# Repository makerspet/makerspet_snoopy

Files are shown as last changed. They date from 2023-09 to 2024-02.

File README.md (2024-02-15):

# Snoopy pet robot



An open-source 300mm DIY 3D-printable pet robot compatible with [Kaia.ai](https://kaia.ai) software [platform](https://github.com/kaiaai/).

Snoopy was designed in Fusion 360 in 05/2023 and printed using a Voron 2.4r2 350mm.

3D print, build, run and mod your own home pet robot! Please learn more at [Maker's Pet](https://makerspet.com).

## Features
- room mapping using a 360-degree laser distance sensor (ROS2-based).
- fully autonomous navigation (ROS2-based).
- code your character, skills (work in progress)
- 3D-printable, 300mm round base
- A smartphone or a 7" tablet acts as a color camera, head display.
- Arduino ESP32 micro-controller.
- optional: 2 bumpers, 4 bumper sensors, 5 cliff sensors.

## Assembly instructions video (Loki, Fido models)
<a href="http://www.youtube.com/watch?feature=player_embedded&v=WPB2B1DPf_s" target="_blank">
 Watch the assembly instructions video
</a>

## PC, firmware setup instructions video
<a href="http://www.youtube.com/watch?feature=player_embedded&v=XOc5kCE3MC0" target="_blank">
 Watch the one-time PC setup, firmware upload instructions video
</a>

## Bring-up instructions video
<a href="http://www.youtube.com/watch?feature=player_embedded&v=L_XbkA4pwRc" target="_blank">
 Watch the bring-up instructions video
</a>

## 3D printing instructions
<a href="http://www.youtube.com/watch?feature=player_embedded&v=4k6W1QyJMMw" target="_blank">
 Watch the bring-up instructions video
</a>

## Arduino ESP32 breakout board setup instructions
<a href="http://www.youtube.com/watch?feature=player_embedded&v=zizGI8MjANU" target="_blank">
 Watch the Arduino ESP32 breakout board setup instructions video
</a>



PXL_20230609_174802983-scaled

PXL_20230530_031143988-scaled

PXL_20230530_021024946-scaled

## Instructions and files
- 3D printing [STL](https://github.com/makerspet/3d_models/tree/main/snoopy_300mm/stl), [3MF](https://github.com/makerspet/3d_models/tree/main/snoopy_300mm/3mf)
- Arduino ESP32 [firmware](https://github.com/kaiaai/firmware)
- PC end user and developer [setup](https://github.com/kaiaai/docker)
- KiCad [schematic, PCB](https://github.com/makerspet/pcb)
- Software setup, configuration [instructions](https://www.youtube.com/playlist?list=PLOSXKDW70aR8SA16wTB0ou9ClKhv7micy)
- Fusion 360 3D CAD [design files](https://github.com/makerspet/3d_models/tree/main/snoopy_300mm/fusion360)
- ROS2 software mod [instructions](https://github.com/makerspet/makerspet_loki/tree/main/urdf)

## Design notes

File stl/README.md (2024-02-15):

Please find 3D model files here https://github.com/makerspet/3d_models/tree/main/snoopy_300mm/stl/.

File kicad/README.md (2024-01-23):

Please find PCB files here https://github.com/makerspet/pcb/.

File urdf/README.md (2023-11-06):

# Maker's Pet Snoopy robot model and configurations

## Modding the robot
- Clone `makerspet_snoopy` robot into a new `jacks_droid` robot.
```
cp -r /ros_ws/src/makerspet_snoopy /ros_ws/src/jacks_droid
rm -rf /ros_ws/src/jacks_droid/.git
```
- Edit `jacks_droid/package.xml` to update the author, website, description, version, email
- Edit `jacks_droid/README.md` to update the description
- Edit `jacks_droid/sdf/jacks_droid/model.config` to update the author, description, version, email
- If needed, edit the robot config files in `jacks_robot/config/`
- If needed, edit the robot model in `jacks_droid/urdf/robot.urdf.xacro`
- Regenerate your simulation model and compile your `jacks_droid` description
```
ros2 run kaiaai_gazebo urdf2sdf.sh /ros_ws/src/jacks_droid
cd /ros_ws
colcon build --symlink-install --packages-select jacks_droid
```

## Command cheat sheet

Operate a modded pet robot residing in `jacks_droid` repo:

```
# Launch the physical robot
ros2 launch kaiaai_bringup physical.launch.py robot_model:=jacks_droid

# Monitor robot's sensors
ros2 launch kaiaai_bringup rviz2.launch.py robot_model:=jacks_droid

# Launch the robot in a simulation - drive manually or let it self-drive
ros2 launch kaiaai_gazebo world.launch.py robot_model:=jacks_droid
ros2 run kaiaai_teleop teleop_keyboard robot_model:=jacks_droid
ros2 launch kaiaai_gazebo self_drive_gazebo.launch.py robot_model:=jacks_droid
ros2 launch kaiaai_bringup rviz2.launch.py robot_model:=jacks_droid

# Launch the robot in a simulation - create, save a map
ros2 launch kaiaai_gazebo world.launch.py robot_model:=jacks_droid
ros2 launch kaiaai_bringup cartographer.launch.py use_sim_time:=true robot_model:=jacks_droid
ros2 launch kaiaai_gazebo self_drive_gazebo.launch.py robot_model:=jacks_droid
ros2 run nav2_map_server map_saver_cli -f $HOME/my_map

# Launch the robot in a simulation - let it navigate automatically using an existing map
ros2 launch kaiaai_gazebo world.launch.py robot_model:=jacks_droid
ros2 launch kaiaai_bringup navigation.launch.py use_sim_time:=true map:=$HOME/my_map.yaml robot_model:=jacks_droid

# Inspect or edit robot's URDF model - useful when modding a robot
ros2 launch kaiaai_bringup inspect_urdf.launch.py robot_model:=jacks_droid
ros2 launch kaiaai_bringup edit_urdf.launch.py robot_model:=jacks_droid

# Convert URDF robot model file into SDF Gazebo simulation model file
ros2 run kaiaai_gazebo urdf2sdf.sh /ros_ws/src/jacks_droid
cd /ros_ws && colcon build --symlink-install --packages-select jacks_droid
```

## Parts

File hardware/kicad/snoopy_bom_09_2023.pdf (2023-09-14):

Maker's Pet Snoopy | https://makerspet.com Electronics BOM, version 9/2023
# | ReferenceQty Value | Footprint DNP | URL

1 J1 | 1 JST PH 8-pin male
2 J2, J5 | 2 JST XH 5-pin male
3 J3 | 1 Deans T-Plug Male | https://www.aliexpress.us/item/2251832807355213.html
4 R1, R3 | 2 10k | 603
5 R5 | 1 200k | 603
6 R6 | 1 100k | 603
7 U1 | 1 ESP32 DEV KIT DOIT 30-pin
8 U2 | 1 MH-KC24 | USB step-down module 24V dual output | https://www.aliexpress.us/item/3256802247317350.html

EXTERNAL COMPONENTS
1 | 2 CHR-GM25-BLDC2418 | BLDC motors 2.5W 190RPM rated 0.35A stall https://www.aliexpress.us/item/2251832633601682.html
2 | 1 YDLIDAR X4 | Laser distance scanner | https://www.ydlidar.com/
3 1 24V battery, Deans T-Plug Female plug Alcaline non-reusable or lithium 6S >=5A load

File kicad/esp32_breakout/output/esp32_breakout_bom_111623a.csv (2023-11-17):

Source: | C:\Users\ilya\git\snoopy\kicad\esp32_breakout\esp32_breakout.kicad_sch
Date: | 11/16/2023 7:33:45 PM
Tool: | Eeschema 7.0.9
Generator: | C:\Program Files\KiCad\7.0\bin\scripting\plugins/bom_csv_grouped_by_value_with_fp.py
Component Count: | 30
Ref | Qnty | Value | Cmp name | Footprint | Description | Vendor | DNP
D1 | 1 | CGRA4004-G | D | Diode_SMD:D_SMA | Diode
H1, H2, H3, H4 | 4 | MountingHole | MountingHole | MountingHole:MountingHole_3.2mm_M3 | Mounting Hole without connection
J1, J2 | 2 | JST PH F | Conn_01x05 | Connector_JST:JST_PH_B5B-PH-K_1x05_P2.00mm_Vertical | Generic connector, single row, 01x05, script generated (kicad-library-utils/schlib/autogen/connector/)
J3 | 1 | JST PH F | Conn_01x07 | Connector_JST:JST_PH_B7B-PH-K_1x07_P2.00mm_Vertical | Generic connector, single row, 01x07, script generated (kicad-library-utils/schlib/autogen/connector/)
J4 | 1 | DC-005 5.5x2.1mm | Barrel_Jack_Switch | Connector_BarrelJack:BarrelJack_GCT_DCJ200-10-A_Horizontal | DC Barrel Jack with an internal switch
J5 | 1 | Deans T-Plug M | Deans T-Plug | Makerspet:DEANS-T-PLUG
J6 | 1 | Header F | Conn_02x04_Top_Bottom | Connector_PinHeader_2.54mm:PinHeader_2x04_P2.54mm_Vertical | Generic connector, double row, 02x04, top/bottom pin numbering scheme (row 1: 1...pins_per_row, row2: pins_per_row+1 ... num_pins), script generated (kicad-library-utils/schlib/autogen/connector/)
J7 | 1 | Header F | Conn_01x05 | Connector_PinHeader_2.54mm:PinHeader_1x05_P2.54mm_Vertical | Generic connector, single row, 01x05, script generated (kicad-library-utils/schlib/autogen/connector/)
J8 | 1 | Header F | Conn_01x03 | Connector_PinHeader_2.54mm:PinHeader_1x03_P2.54mm_Vertical | Generic connector, single row, 01x03, script generated (kicad-library-utils/schlib/autogen/connector/)
J9, J10, J11 | 3 | JST PH F | Conn_01x06 | Connector_JST:JST_PH_B6B-PH-K_1x06_P2.00mm_Vertical | Generic connector, single row, 01x06, script generated (kicad-library-utils/schlib/autogen/connector/)
Q1 | 1 | BSS123 | BSS123 | Package_TO_SOT_SMD:SOT-23 | 0.17A Id, 100V Vds, N-Channel MOSFET, SOT-23
R1, R2, R3, R4, R6, R7 | 6 | 10k | R_Small_US | Resistor_SMD:R_0603_1608Metric | Resistor, small US symbol
R5 | 1 | 1k | R_Small_US | Resistor_SMD:R_0603_1608Metric | Resistor, small US symbol
R8 | 1 | 200k | R_Small_US | Resistor_SMD:R_0603_1608Metric | Resistor, small US symbol
R9 | 1 | 100k | R_Small_US | Resistor_SMD:R_0603_1608Metric | Resistor, small US symbol
R10 | 1 | 4.7k | R_Small_US | Resistor_SMD:R_0603_1608Metric | Resistor, small US symbol
SW1 | 1 | SS12D10 | SW_SPDT | Makerspet:SWITCH | Switch, single pole double throw
U1 | 1 | ESP32 DEV KIT 30-pin | ESP32-DOIT-V1 | Makerspet:ESP-32
U2 | 1 | Mini560-Pro | DC-DC | Makerspet:Mini560-Pro

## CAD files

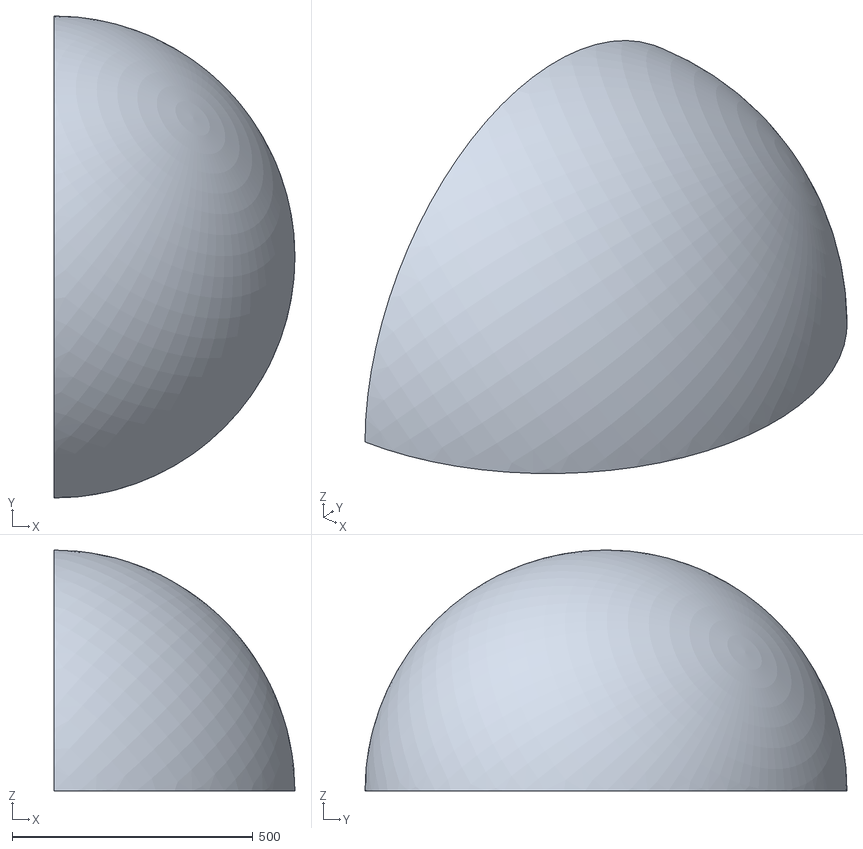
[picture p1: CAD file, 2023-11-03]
sdf/makerspet_snoopy/mesh/quarter_sphere.stl
500.0 x 1000.0 x 500.0

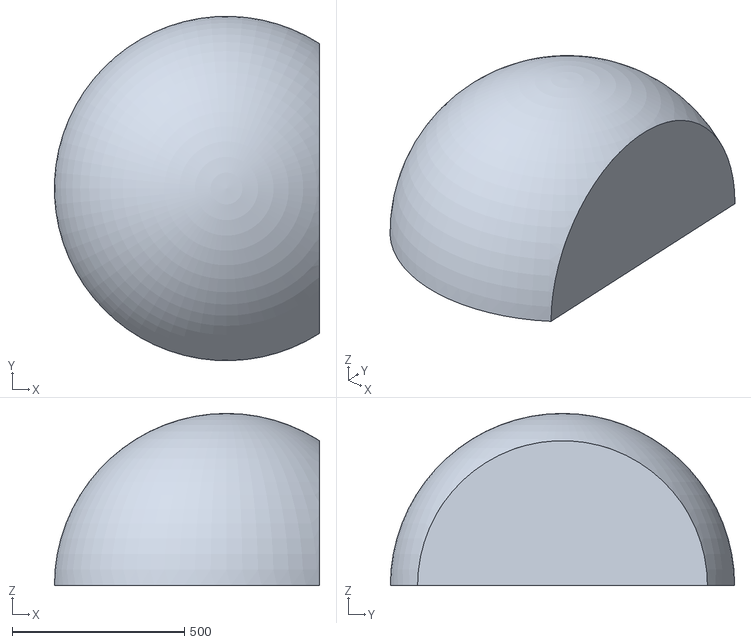
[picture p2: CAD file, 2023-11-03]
sdf/makerspet_snoopy/mesh/head.stl
769.5 x 999.7 x 500.0

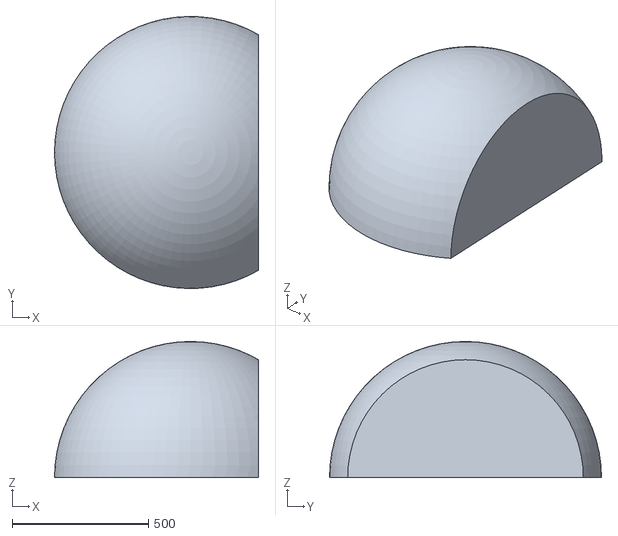
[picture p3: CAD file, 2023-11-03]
sdf/makerspet_snoopy/mesh/quarter_sphere_250mm.stl
750.0 x 999.7 x 500.0

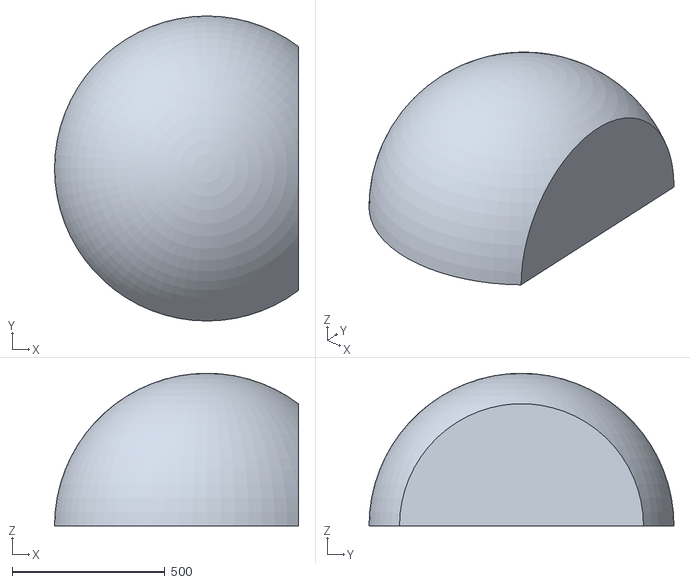
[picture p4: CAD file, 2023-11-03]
sdf/makerspet_snoopy/mesh/quarter_sphere_300mm.stl
800.0 x 1000.0 x 500.0

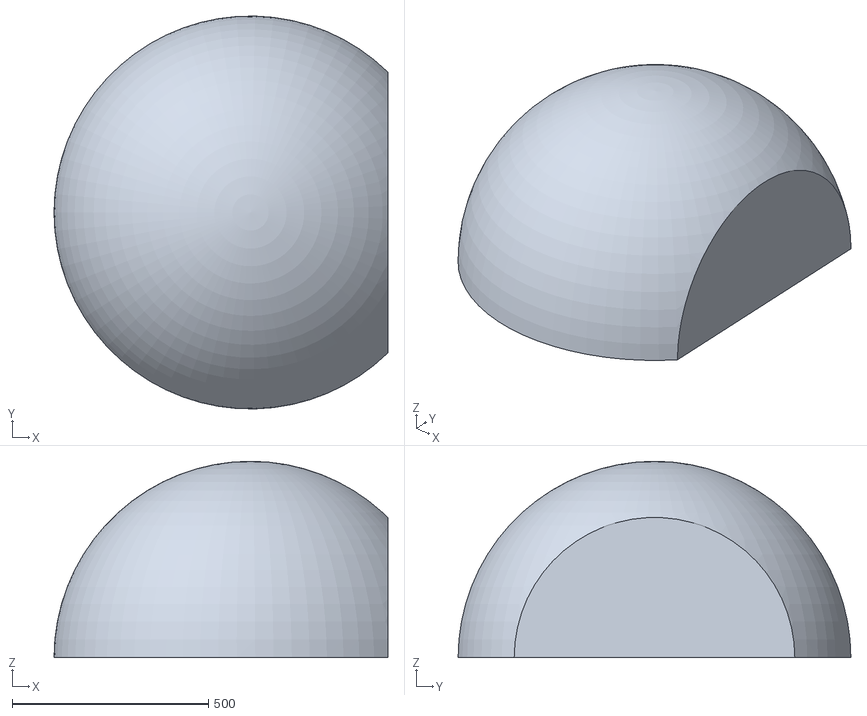
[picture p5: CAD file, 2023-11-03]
sdf/makerspet_snoopy/mesh/quarter_sphere_350mm.stl
850.0 x 999.7 x 500.0

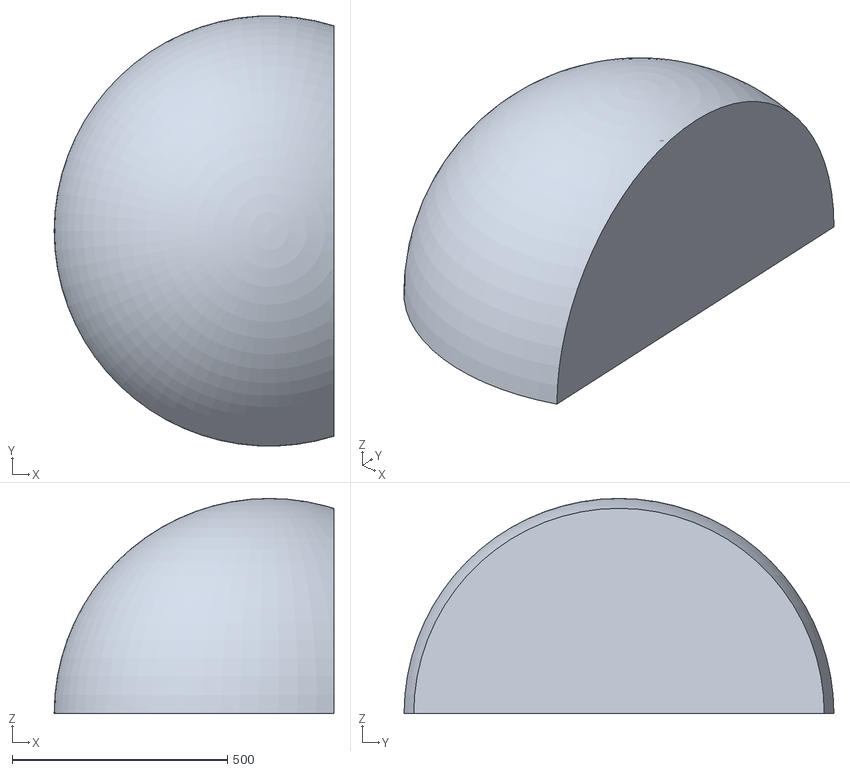
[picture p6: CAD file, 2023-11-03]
sdf/makerspet_snoopy/mesh/quarter_sphere_150mm.stl
650.0 x 999.3 x 500.0

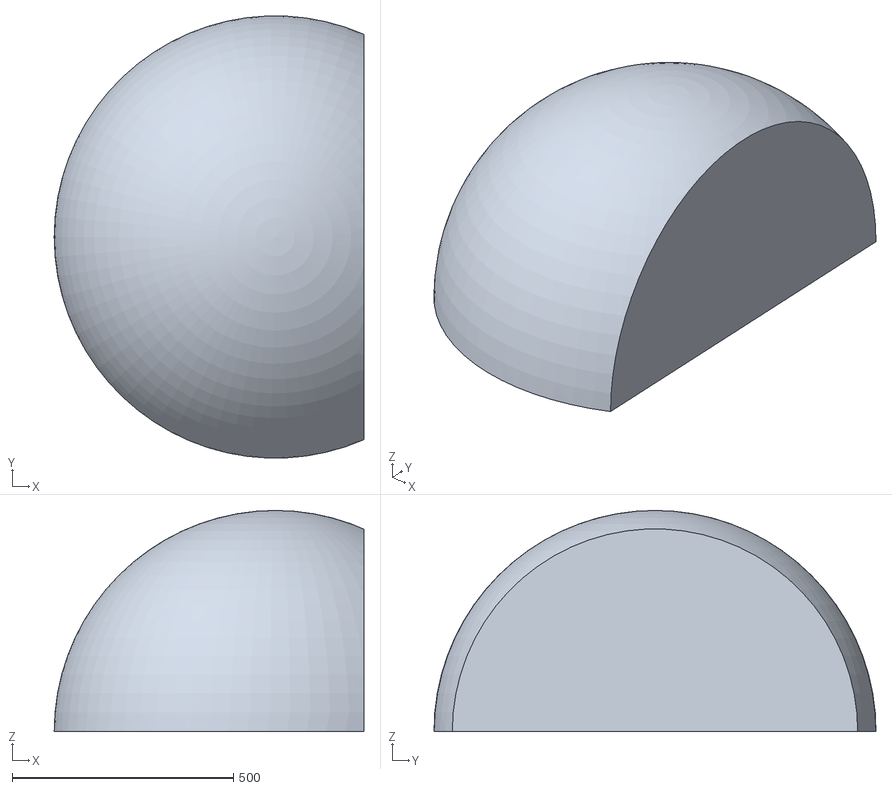
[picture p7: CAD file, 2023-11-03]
sdf/makerspet_snoopy/mesh/quarter_sphere_200mm.stl
700.0 x 999.2 x 500.0

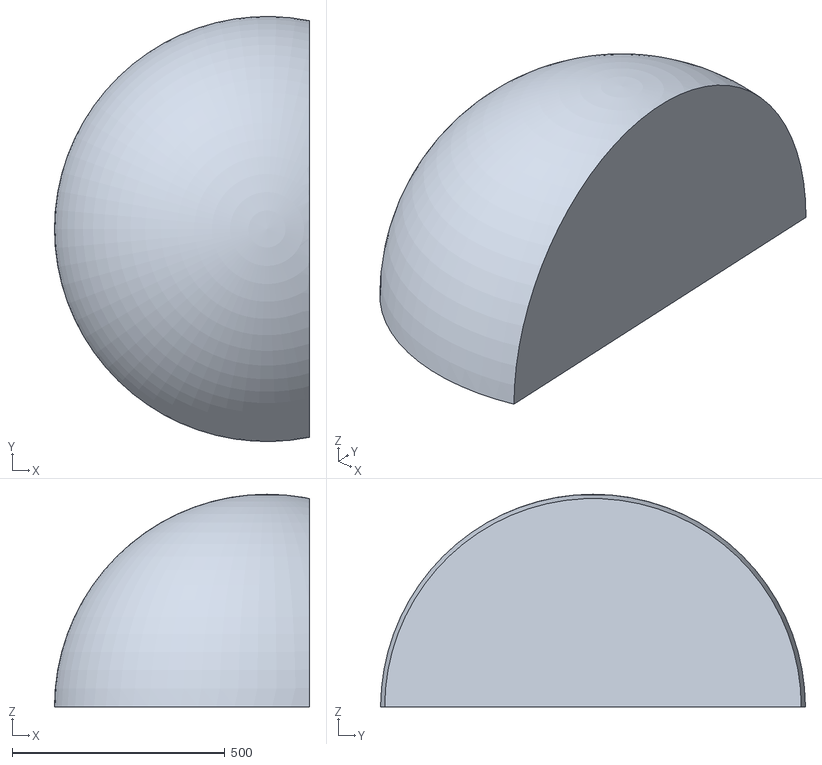
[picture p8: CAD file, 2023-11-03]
sdf/makerspet_snoopy/mesh/quarter_sphere_100mm.stl
600.0 x 999.7 x 500.0

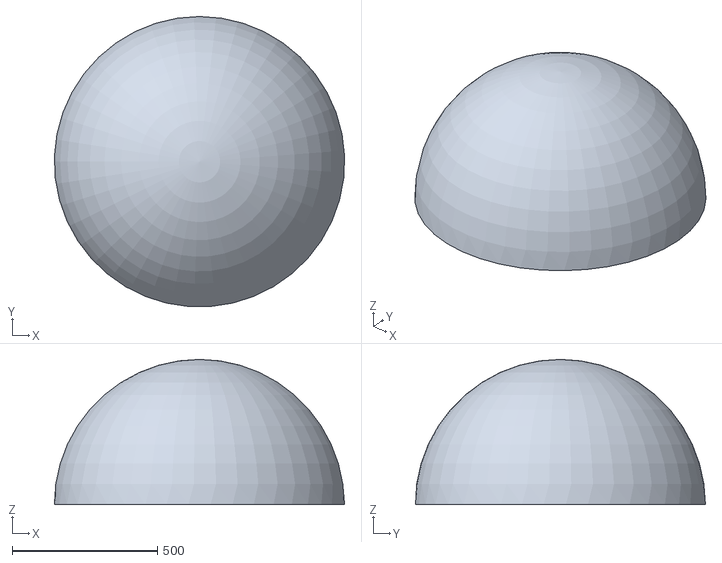
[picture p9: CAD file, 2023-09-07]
sdf/makerspet_snoopy/mesh/half_sphere.stl
999.3 x 998.5 x 500.0

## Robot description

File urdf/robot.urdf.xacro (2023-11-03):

<?xml version="1.0" ?>
<robot name="makerspet_snoopy" xmlns:xacro="http://ros.org/wiki/xacro">
  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
  <xacro:property name="wheel_diameter" value="0.067"/>
  <xacro:property name="wheel_width" value="0.029"/>
  <xacro:property name="caster_diameter" value="0.042"/>
  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
  <xacro:property name="caster_inset" value="0.0405"/>
  <xacro:property name="floor_clearance" value="0.018"/>
  <xacro:property name="base_diameter" value="0.300"/>
  <xacro:property name="wheel_base" value="0.262794"/>
  <xacro:property name="lower_cylinder_height" value="0.119"/>
  <xacro:property name="lower_to_upper_cylinders_gap" value="0.026"/>
  <xacro:property name="laser_puck_to_upper_cylinder_gap" value="0.005"/>
  <xacro:property name="laser_puck_diameter" value="0.0656"/>
  <xacro:property name="upper_cylinder_height" value="0.013"/>
  <xacro:property name="head_height" value="0.104"/>
  <xacro:property name="tablet_width" value="0.1669"/>
  <xacro:property name="tablet_height" value="0.0781"/>
  <xacro:property name="tablet_thickness" value="0.009"/>
  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
  <xacro:property name="tablet_pitch_angle" value="20"/>
  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
  <xacro:property name="tablet_inset" value="0.0355"/>
  <xacro:property name="color_camera_diameter" value="0.004"/>
  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
  <xacro:property name="color_camera_inset" value="0.008"/>
  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
  <xacro:property name="imu_joint_dx" value="0"/>
  <xacro:property name="imu_joint_dy" value="0"/>
  <xacro:property name="imu_joint_dz" value="0"/>
  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

  <xacro:property name="motor_stall_torque" value="0.49"/>
  <xacro:property name="max_wheel_acceleration" value="5"/>
  <xacro:property name="lower_cylinder_mass" value="0.500"/>
  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
  <xacro:property name="caster_mass" value="0.120"/>
  <xacro:property name="wheel_mass" value="0.050"/>
  <xacro:property name="laser_puck_mass" value="0.200"/>
  <xacro:property name="upper_cylinder_mass" value="0.100"/>
  <xacro:property name="head_mass" value="0.200"/>
  <xacro:property name="tablet_mass" value="0.200"/>
  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

  <xacro:property name="DEG2RAD" value="0.0174533"/>
  <xacro:property name="color_camera_thickness" value="0.0001"/>
  <xacro:property name="imu_xlen" value="0.001"/>
  <xacro:property name="imu_ylen" value="0.002"/>
  <xacro:property name="imu_zlen" value="0.004"/>

  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

  <xacro:macro name="solid_box_inertia" params="m x y z">
    <inertial>
      <origin xyz="0 0 0" rpy="${pi/2} 0 ${pi/2}"/>
      <mass value="${m}"/>
      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
    </inertial>
  </xacro:macro>

  <xacro:macro name="solid_cylinder_inertia" params="m r h">
    <inertial>
      <origin xyz="0 0 0" rpy="${pi/2} 0 0" />
      <mass value="${m}"/>
      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
    </inertial>
  </xacro:macro>

  <xacro:macro name="hollow_cylinder_inertia" params="m ri ro h">
    <inertial>
      <origin xyz="0 0 0" rpy="${pi/2} 0 0" />
      <mass value="${m}"/>
      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
    </inertial>
  </xacro:macro>

  <xacro:macro name="thin_cylindrical_shell_inertia" params="m r h">
    <inertial>
      <origin xyz="0 0 0" rpy="${pi/2} 0 0" />
      <mass value="${m}"/>
      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
    </inertial>
  </xacro:macro>

  <xacro:macro name="solid_sphere_inertia" params="m r">
    <inertial>
      <mass value="${m}"/>
      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
    </inertial>
  </xacro:macro>

  <xacro:macro name="thin_spherical_shell_inertia" params="m r">
    <inertial>
      <mass value="${m}"/>
      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
    </inertial>
  </xacro:macro>

  <xacro:macro name="solid_hemisphere_inertia" params="m r">
    <inertial>
      <mass value="${m}"/>
      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
    </inertial>
  </xacro:macro>

  <xacro:macro name="solid_ellipsoid_inertia" params="m x y z">
    <inertial>
      <mass value="${m}"/>
      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
    </inertial>
  </xacro:macro>

  <xacro:macro name="solid_semi_ellipsoid_inertia" params="m x y z">
    <inertial>
      <mass value="${m}"/>
      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
    </inertial>
  </xacro:macro>

  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

  <link name="base_footprint"/>

  <joint name="base_joint" type="fixed">
    <parent link="base_footprint"/>
    <child link="base_link"/>
    <origin xyz="0 0 ${floor_clearance}" rpy="0 0 0"/>
  </joint>

  <link name="base_link">
    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

    <xacro:solid_cylinder_inertia m="${lower_cylinder_mass}" r="${base_diameter/2}" h="${lower_cylinder_height}"/>
  </link>


  <joint name="caster_joint" type="fixed">
    <parent link="base_link"/>
    <child link="caster_link"/>
    <origin xyz="${base_diameter/2-caster_inset} 0 ${caster_diameter/2-floor_clearance}" rpy="0 0 0"/>
  </joint>

  <link name="caster_link">
    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

    <xacro:solid_sphere_inertia m="${caster_mass}" r="${caster_diameter/2}"/>
  </link>


  <joint name="wheel_left_joint" type="continuous">
    <parent link="base_link"/>
    <child link="wheel_left_link"/>
    <origin xyz="0 ${wheel_base/2} ${wheel_diameter/2-floor_clearance}" rpy="-${pi/2} 0 0"/>
    <axis xyz="0 0 1"/>
  </joint>

  <link name="wheel_left_link">
    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

    <xacro:solid_cylinder_inertia m="${wheel_mass}" r="${wheel_diameter/2}" h="${wheel_width}"/>
  </link>

  <joint name="wheel_right_joint" type="continuous">
    <parent link="base_link"/>
    <child link="wheel_right_link"/>
    <origin xyz="0 ${-wheel_base/2} ${wheel_diameter/2-floor_clearance}" rpy="-${pi/2} 0 0"/>
    <axis xyz="0 0 1"/>
  </joint>

  <link name="wheel_right_link">
    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

    <xacro:solid_cylinder_inertia m="${wheel_mass}" r="${wheel_diameter/2}" h="${wheel_width}"/>
  </link>


  <joint name="scan_joint" type="fixed">
    <parent link="base_link"/>
    <child link="base_scan"/>
    <origin xyz="0 0 ${lower_cylinder_height + (lower_to_upper_cylinders_gap - laser_puck_to_upper_cylinder_gap)/2}" rpy="-${pi} 0 0"/>
  </joint>

  <link name="base_scan">
    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

    <xacro:solid_cylinder_inertia m="${laser_puck_mass}" r="${laser_puck_diameter/2}" h="${lower_to_upper_cylinders_gap - laser_puck_to_upper_cylinder_gap}"/>
  </link>


  <joint name="base_upper_joint" type="fixed">
    <parent link="base_link"/>
    <child link="base_upper_link"/>
    <origin xyz="0 0 ${lower_cylinder_height + lower_to_upper_cylinders_gap}" rpy="0 0 0"/>
  </joint>

  <link name="base_upper_link">
    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

    <xacro:solid_cylinder_inertia m="${upper_cylinder_mass}" r="${base_diameter/2}" h="${upper_cylinder_height}"/>
  </link>


  <joint name="head_joint" type="fixed">
    <parent link="base_upper_link"/>
    <child link="head_link"/>
    <origin xyz="0 0 ${upper_cylinder_height}" rpy="0 0 0"/>
  </joint>

  <link name="head_link">
    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

    <xacro:solid_semi_ellipsoid_inertia m="${head_mass}" x="${base_diameter/2}" y="${base_diameter/2}" z="${head_height}"/>
  </link>


  <joint name="tablet_joint" type="fixed">
    <parent link="head_link"/>
    <child link="tablet_link"/>
    <origin xyz="${base_diameter/2 - tablet_inset} 0 0" rpy="0 ${-tablet_pitch_angle*DEG2RAD} 0"/>
  </joint>

  <link name="tablet_link">
    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

    <xacro:solid_box_inertia m="${tablet_mass}" x="${tablet_width}" y="${tablet_height}" z="${tablet_thickness}"/>
  </link>

  <joint name="color_camera_joint" type="fixed">
    <parent link="tablet_link"/>
    <child link="color_camera_link"/>
    <origin xyz="${tablet_thickness/2-color_camera_thickness} ${color_camera_inset - tablet_width/2} ${tablet_height/2}" rpy="0 0 0"/>
  </joint>

  <link name="color_camera_link">
    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
  </link>


  <joint name="imu_joint" type="fixed">
    <parent link="tablet_link"/>
    <child link="imu_link"/>
    <origin xyz="${imu_joint_dx} ${imu_joint_dy} ${imu_joint_dz+tablet_height/2}" rpy="0 0 0"/>
  </joint>

  <link name="imu_link">
    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
  </link>

  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
</robot>

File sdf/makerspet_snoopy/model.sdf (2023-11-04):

<sdf version='1.7'>
  <model name='makerspet_snoopy'>
    <link name='base_footprint'>
      <inertial>
        <pose>0.027303 0 0.096758 0 -0 0</pose>
        <mass>1.32</mass>
        <inertia>
          <ixx>0.0125249</ixx>
          <ixy>-1.23224e-19</ixy>
          <ixz>-0.000786958</ixz>
          <iyy>0.0179806</iyy>
          <iyz>-8.40834e-19</iyz>
          <izz>0.00850298</izz>
        </inertia>
      </inertial>
      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
      <sensor name='color_camera' type='camera'>
        <always_on>1</always_on>
        <visualize>0</visualize>
        <update_rate>15</update_rate>
        <camera name='front_color_camera'>
          <horizontal_fov>1.39626</horizontal_fov>
          <image>
            <width>720</width>
            <height>480</height>
            <format>R8G8B8</format>
          </image>
          <clip>
            <near>0.02</near>
            <far>300</far>
          </clip>
          <noise>
            <type>gaussian</type>
            <mean>0</mean>
            <stddev>0.007</stddev>
          </noise>
        </camera>
        <plugin name='color_camera_plugin' filename='libgazebo_ros_camera.so'/>
        <pose>0.105279 -0.07545 0.2142 0 -0.349066 0</pose>
      </sensor>
      <gravity>1</gravity>
      <sensor name='imu_sensor' type='imu'>
        <always_on>1</always_on>
        <update_rate>100</update_rate>
        <imu>
          <angular_velocity>
            <x>
              <noise type='gaussian'>
                <mean>0</mean>
                <stddev>0.0002</stddev>
              </noise>
            </x>
            <y>
              <noise type='gaussian'>
                <mean>0</mean>
                <stddev>0.0002</stddev>
              </noise>
            </y>
            <z>
              <noise type='gaussian'>
                <mean>0</mean>
                <stddev>0.0002</stddev>
              </noise>
            </z>
          </angular_velocity>
          <linear_acceleration>
            <x>
              <noise type='gaussian'>
                <mean>0</mean>
                <stddev>0.017</stddev>
              </noise>
            </x>
            <y>
              <noise type='gaussian'>
                <mean>0</mean>
                <stddev>0.017</stddev>
              </noise>
            </y>
            <z>
              <noise type='gaussian'>
                <mean>0</mean>
                <stddev>0.017</stddev>
              </noise>
            </z>
          </linear_acceleration>
        </imu>
        <plugin name='imu_plugin' filename='libgazebo_ros_imu_sensor.so'>
          <ros>
            <remapping>~/out:=imu</remapping>
          </ros>
        </plugin>
        <pose>0.101144 0 0.212695 0 -0.349066 0</pose>
      </sensor>
      <sensor name='laser_scan_sensor' type='ray'>
        <visualize>0</visualize>
        <always_on>1</always_on>
        <update_rate>9</update_rate>
        <ray>
          <scan>
            <horizontal>
              <samples>360</samples>
              <resolution>1</resolution>
              <min_angle>0</min_angle>
              <max_angle>6.28319</max_angle>
            </horizontal>
          </scan>
          <range>
            <min>0.1</min>
            <max>12</max>
            <resolution>0.02</resolution>
          </range>
          <noise>
            <type>gaussian</type>
            <mean>0</mean>
            <stddev>0.01</stddev>
          </noise>
        </ray>
        <plugin name='laser_scan_plugin' filename='libgazebo_ros_ray_sensor.so'>
          <ros>
            <remapping>~/out:=scan</remapping>
          </ros>
          <output_type>sensor_msgs/LaserScan</output_type>
          <frame_name>base_scan</frame_name>
        </plugin>
        <pose>0 0 0.1475 -3.14159 0 0</pose>
      </sensor>
    </link>
    <joint name='wheel_left_joint' type='revolute'>
      <pose relative_to='base_footprint'>0 0.131397 0.0335 -1.5708 0 0</pose>
      <parent>base_footprint</parent>
      <child>wheel_left_link</child>
      <axis>
        <xyz>0 0 1</xyz>
        <limit>
          <lower>-1e+16</lower>
          <upper>1e+16</upper>
        </limit>
        <dynamics>
          <spring_reference>0</spring_reference>
          <spring_stiffness>0</spring_stiffness>
        </dynamics>
      </axis>
    </joint>
    <link name='wheel_left_link'>
      <pose relative_to='wheel_left_joint'>0 0 0 0 -0 0</pose>
      <inertial>
        <pose>0 0 0 1.5708 -0 0</pose>
        <mass>0.05</mass>
        <inertia>
          <ixx>1.75323e-05</ixx>
          <ixy>0</ixy>
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

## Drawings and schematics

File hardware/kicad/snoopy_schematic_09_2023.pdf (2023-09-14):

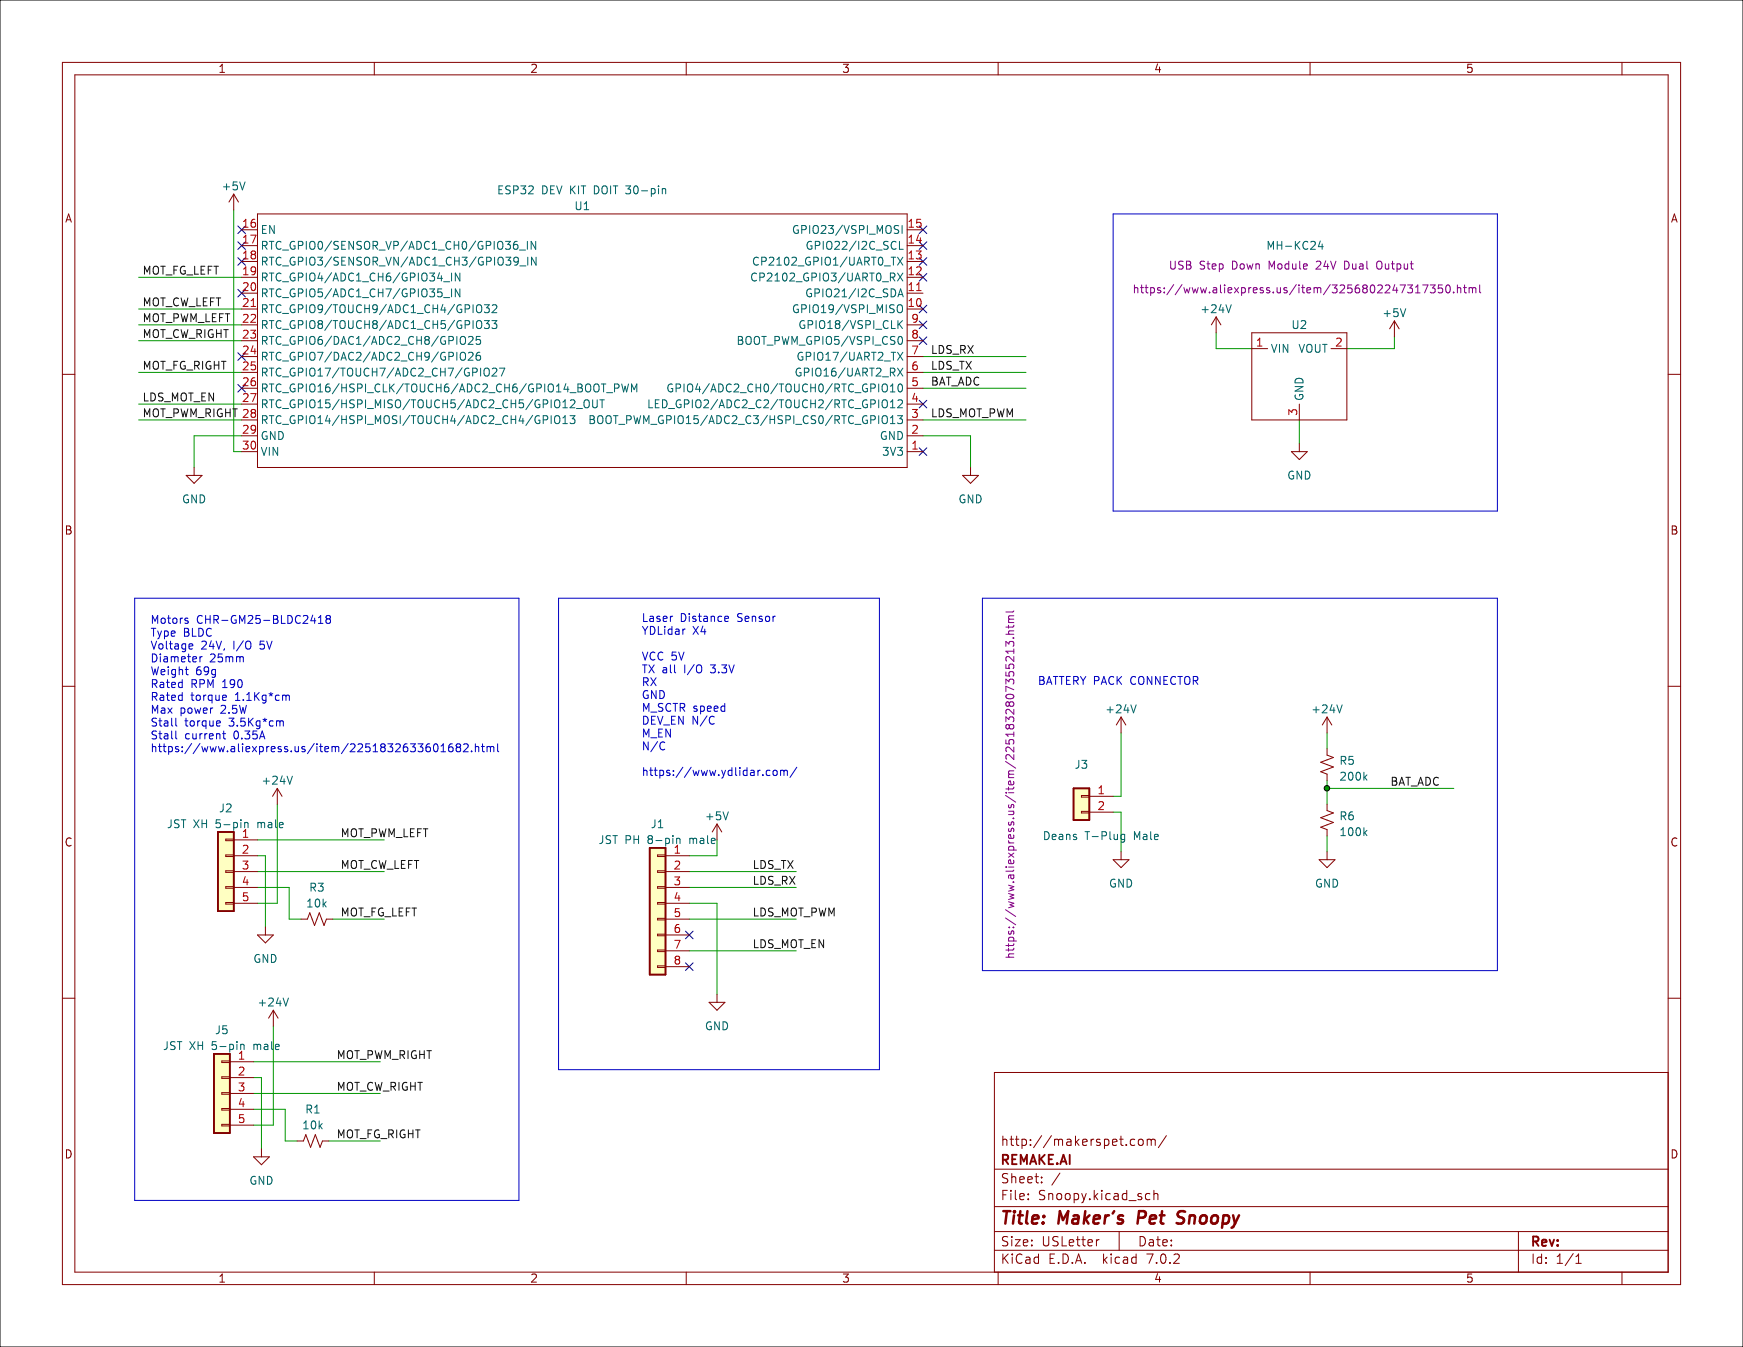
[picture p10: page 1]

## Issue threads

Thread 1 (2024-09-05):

Bumper

g02200jeff, 2024-09-05:
Hi, could you say me if the functionnality of the bumper working now ?

makerspet, 2024-09-06:
Hi,
  not yet. Bumper functionality is on the to-do list for the next product.

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

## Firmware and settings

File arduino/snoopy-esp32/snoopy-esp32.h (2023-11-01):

#ifndef SNOOPY_ESP32
#define SNOOPY_ESP32

// Motors config
#define WHEEL_DIA (2*33.5e-3) // meters
#define WHEEL_BASE (262.794*1e-3) // wheel base, meters
#define MAX_WHEEL_ACCEL 2.0   // wheel vs floor m2/sec

// ESP32 pin assignment
#define LED_PIN 2
#define YD_MOTOR_SCTP_PIN 15 // 2 PWM pin for control the speed of YDLIDAR's motor. 
#define YD_MOTOR_EN_PIN   12 // 15 The ENABLE PIN for YDLIDAR's motor                  
#define YD_MOTOR_SPEED 255  // LEAVE DISCONNECTED
#define YD_MOTOR_SPEED_DEFAULT -1  // disconnect SCTP pin for default motor speed
#define YD_MOTOR_SCTP_PWM_CHANNEL 0  // ESP32 PWM channel

// Micro-ROS config
#define UROS_CLIENT_KEY 0xCA1AA100
#define UROS_TELEM_TOPIC_NAME "telemetry"
#define UROS_LOG_TOPIC_NAME "rosout"
#define UROS_CMD_VEL_TOPIC_NAME "cmd_vel"
#define UROS_NODE_NAME "snoopy_esp32"
#define UROS_PING_PUB_PERIOD_MS 10000
#define UROS_TELEM_PUB_PERIOD_MS 50
#define UROS_TIME_SYNC_TIMEOUT_MS 1000

#define JOINTS_LEN (MOTOR_COUNT)
#define LDS_BUF_LEN 400
#define LDS_SERIAL_BAUD 128000  // YDLIDAR X4

// WiFi config
#define WIFI_CONN_TIMEOUT_SEC 30
#define RESET_SETTINGS_HOLD_SEC 5 // Hold button this long to reset WiFi

// ESP32 blinks when firmware init fails
#define ERR_WIFI_CONN 1
#define ERR_LDS_INIT 2
#define ERR_UROS_AGENT_CONN 3
#define ERR_WIFI_LOST 4
#define ERR_UROS_INIT 5
#define ERR_UROS_NODE 6
#define ERR_UROS_PUBSUB 7
#define ERR_UROS_EXEC 8
#define ERR_UROS_TIME_SYNC 9
#define ERR_UROS_SPIN 10

#define ERR_REBOOT_BLINK_CYCLES 3 // Blinki out an error a few times, then reboot
#define LONG_BLINK_MS 1000
#define LONG_BLINK_PAUSE_MS 2000
#define SHORT_BLINK_MS 200
#define SHORT_BLINK_PAUSE_MS 500

#define TELEM_PUB_PERIOD_MS 50
#define SPIN_TELEM_STATS 100 // Undefine for debug
#define PING_PUB_PERIOD_MS 10000

#if !defined(ESP32)
  #error This code builds on ESP32 Dev module only
#endif

void serial_callback(char c);
void scan_callback(uint8_t quality, float angle_deg,
  float distance_mm, bool startBit);

#endif  // SNOOPY_ESP32

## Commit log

2023-09-07 Repo reord, added ROS2 software
    [head.stl, kaia_snoopy.urdf.xacro, model.sdf]
2023-09-08 hardware folder
    [Bumper sensor assembly(Mirror)_Bumper assembly v43_Bumper bracket side v29(Mirror)_1_Body1.3mf, Bumper sensor assembly_Bumper assembly v43_Bumper bracket cover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]
2023-09-14 Schematic, BOM
    [Servos.kicad_sch, Snoopy.csv, Snoopy.kicad_pcb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]
2023-09-14 T Plug fix
    [Snoopy.csv, Snoopy.kicad_sch]
2023-09-17 Renamed packages
    [head.stl, makerspet_snoopy.urdf.xacro, model.sdf]
2023-09-19 URDF fix
    [makerspet_snoopy.urdf.xacro]
2023-09-22 Turn off ray vis
    [makerspet_snoopy.urdf.xacro, model.sdf]
2023-09-22 Move urdf2sdf.sh
2023-09-22 SDF fix
    [makerspet_snoopy.urdf.xacro, model.sdf]
2023-09-22 Regenerated SDF
    [makerspet_snoopy.urdf.xacro, model.sdf]
2023-09-27 Max motor teleop speed
2023-09-27 Reversed left motor
2023-09-28 Motors seem to work
2023-09-28 URDF wheel base fix
    [makerspet_snoopy.urdf.xacro]
2023-09-28 URDF base fix
    [makerspet_snoopy.urdf.xacro]
2023-09-28 Telem lds frame rename
2023-09-28 Teleop params cleanup
    [makerspet_snoopy.urdf.xacro]
2023-09-28 Fix world frame
2023-09-29 URDF base_scan fix
    [makerspet_snoopy.urdf.xacro]
2023-09-29 Servos, dock, pulldowns
    [Snoopy.kicad_sch]
2023-10-30 PID library
2023-10-30 KiCad PCB work-in-progress
    [Servos.kicad_sch, cliff_sensors.kicad_sch, esp32_breakout.csv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]
2023-11-03 Quarter sphere head
    [head.stl]
2023-11-03 Quarter sphere cuts
    [quarter_sphere_100mm.stl, quarter_sphere_150mm.stl, quarter_sphere_200mm.stl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]
2023-11-03 URDF cmd_vel fix
    [makerspet_snoopy.urdf.xacro, model.sdf]
2023-11-03 Battery weight
    [makerspet_snoopy.urdf.xacro]
2023-11-04 Undo hw,fw folders
    [18650_6s_3x2_battery_holder_v11_1_body1.3mf, 18650_6s_3x2_battery_holder_v11_1_body1.stl, 65mm_tire_1_body1.3mf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]
2023-11-15 KiCad PCB schematic
    [esp32_breakout.kicad_sch]
2023-11-15 Schematic WIP
    [esp32_breakout.kicad_pcb, esp32_breakout.kicad_sch]
2023-11-16 Fix broken fw; ESP32 schematic
    [esp32_breakout.kicad_pcb, esp32_breakout.kicad_sch]
2023-11-16 Layout DRC pass
    [esp32_breakout.kicad_pcb, esp32_breakout.kicad_sch]
2023-11-17 PCB gerber
    [DCJ200-10-A-K1-K--3DModel-STEP-740395.STEP, DC_Power_Jack_PCB_Mounted_2.1mm.step, SS-12D10L4.STEP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]
2023-11-23 3D printing vid
2023-12-01 Schematic, BOM R9 fix
    [esp32_breakout.kicad_sch, esp32_breakout_bom_113023a.csv]
2023-12-16 ESP32 breakout v1.0
    [LM2596 DC-DC StepDown Converter v1.step, SS14LW.step, XT30U-M.step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]
2023-12-16 Raspberry Pi Pico head extension PCB proto
    [pico_breakout_head.kicad_pcb, pico_breakout_head.kicad_sch, pico_breakout_head_bom.csv]
2023-12-17 KiCAD bugfix?
    [pico_breakout_head.kicad_pcb]
2023-12-17 Gerber fix
2023-12-18 Socket header
    [pico_breakout_head.kicad_pcb, pico_breakout_head.kicad_sch, pico_breakout_head_bom.csv]
2023-12-18 ESP32 PCB README files
2023-12-19 ESP32 board v1.1
    [esp32_breakout.kicad_pcb, esp32_breakout.kicad_sch, esp32_breakout_bom.csv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]
2023-12-19 PCB image fix
2023-12-19 PCB image fix again
2023-12-22 LDS02RR adapter PCB
    [LDS02RR_adapter.kicad_pcb, LDS02RR_adapter.kicad_sch, LDS02RR_adapter_BOM.csv]
2023-12-22 Reverted ESP32 PCB to v1
    [esp32_breakout.kicad_pcb, esp32_breakout.kicad_sch, esp32_breakout_bom.csv]
2023-12-22 Pico head PCB 0.1.1
    [LDS02RR_adapter.step, pico_breakout_head.kicad_pcb, pico_breakout_head.kicad_sch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]
2023-12-24 Footprint fix
    [esp32_breakout.kicad_pcb, esp32_breakout.kicad_sch, esp32_breakout_bom.csv]
2023-12-26 Alt fuse; fan fix
    [esp32_breakout.kicad_pcb, esp32_breakout.kicad_sch, pico_breakout_head.kicad_pcb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]
2023-12-29 ESP32 PCB v1.1.0
    [JST-B10B-ZR.step, JST-B11B-ZR.step, JST-B12B-ZR.step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]
2023-12-29 Single GPIO header
    [esp32_breakout.kicad_pcb, esp32_breakout.kicad_sch, esp32_breakout_bom.csv]
2023-12-31 PCB hole, sonar tweaks
    [esp32_breakout.kicad_pcb, esp32_breakout.kicad_sch, esp32_breakout_bom.csv]
2024-01-12 LDS02RR PCB README
2024-01-21 Neato LDS adapter schematic
    [Neato_adapter.kicad_sch, Neato_adapter_bom.csv]
2024-01-21 Neato adapter PCB Gerber
    [Neato_adapter.kicad_pcb, Neato_adapter.kicad_sch, Neato_adapter_bom.csv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]
2024-01-23 Moved PCB to dedicated repo
    [DCJ200-10-A-K1-K--3DModel-STEP-740395.STEP, DC_Power_Jack_PCB_Mounted_2.1mm.step, JST-B10B-ZR.step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]
2024-02-15 Moved 3D models to a separate repo
    [18650_6s_3x2_battery_holder_v11_1_body1.3mf, 18650_6s_3x2_battery_holder_v11_1_body1.stl, 65mm_tire_1_body1.3mf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]
